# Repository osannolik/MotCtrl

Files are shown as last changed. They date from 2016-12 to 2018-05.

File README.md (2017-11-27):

MotCtrl
=========================== 

A small inverter for brushless motors. 

## Hardware

* Microcontroller STM32F446, ARM Cortex-M4, 180 MHz, FPU
* Power MOSFETs 60 V, 300 A, 1.1 mOhm FDBL0110N60
* High- and low-side gate drivers LM5101A
* Inline phase current sensing using INA240 amplifiers
* Hall-sensor inputs
* Standard servo (PPM/PWM) input
* Motor and board temp sensor (NTC)
* Expansion header for UART/ADC/DAC/SPI/I2C/CAN
* PCB size 45x77 mm

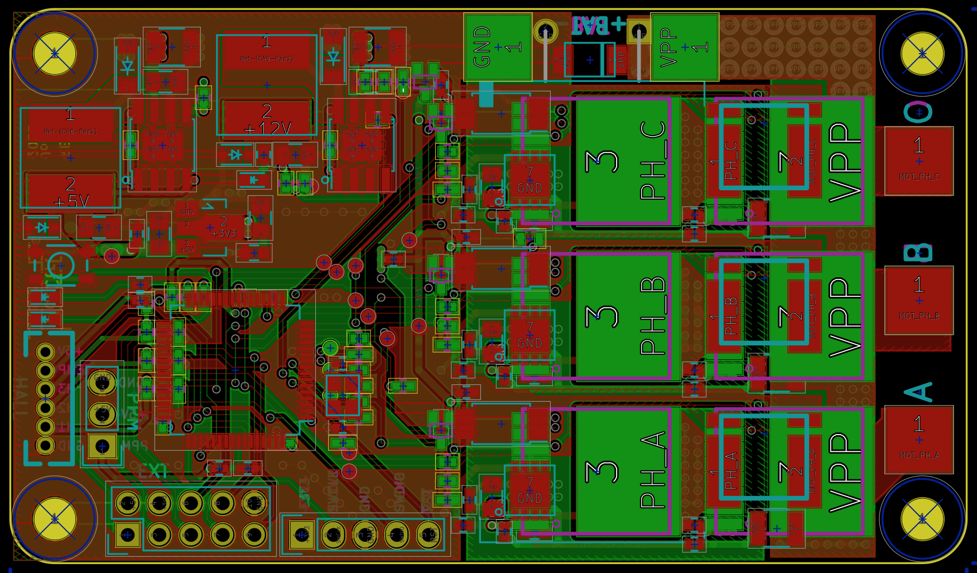
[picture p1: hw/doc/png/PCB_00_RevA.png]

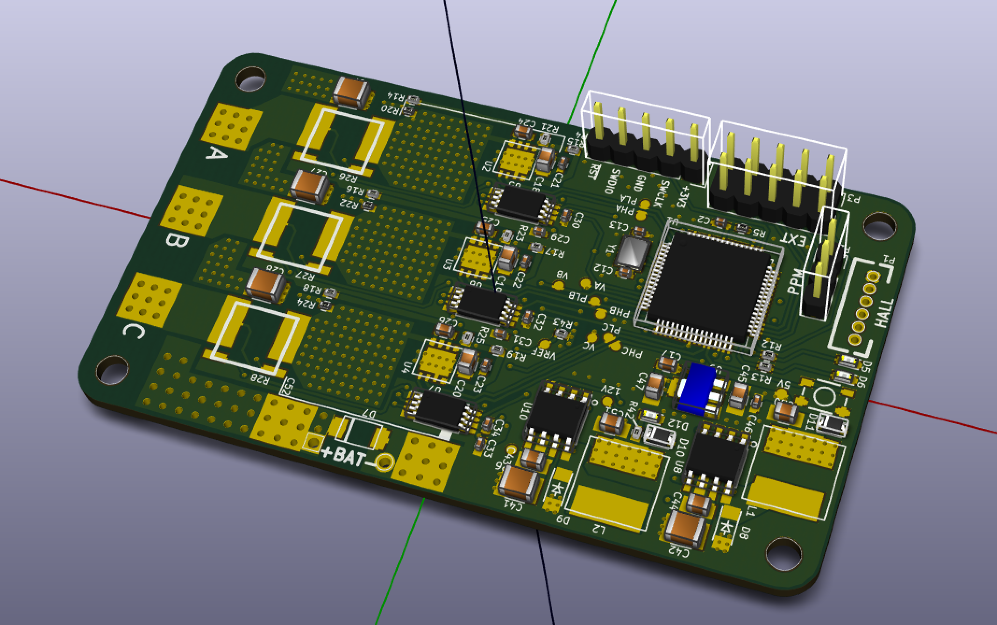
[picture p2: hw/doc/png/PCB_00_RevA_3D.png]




# License
GNU GPLv3 (both hardware and experimental software)

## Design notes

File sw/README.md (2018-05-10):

# Software
This software should be seen as a proof of concept, or as a starting point for developing a complete motor control application.

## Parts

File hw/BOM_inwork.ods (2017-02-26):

Reference | Value | Qty | Digikey | Package
C1 | 10n |  | 1276-1051-1-ND | 0402
C10 | 100n |  | 1276-1001-1-ND | 0402
C11 | 100n |  | 1276-1001-1-ND | 0402
C12 | np |  |  | 0402
C13 | np |  |  | 0402
C14 | 100n |  | 1276-1001-1-ND | 0402
C15 | 100n |  | 1276-1001-1-ND | 0402
C16 | 100n |  | 1276-1001-1-ND | 0402
C17 | 4u7 |  | 1276-2087-1-ND | 0603
C18 | 10u |  | 1276-2872-1-ND | 0805
C19 | 10u |  | 1276-2872-1-ND | 0805
C2 | 4n7 |  | 490-8259-1-ND | 0402
C20 | 10u |  | 1276-2872-1-ND | 0805
C21 | 100n |  | 1276-1001-1-ND | 0402
C22 | 100n |  | 1276-1001-1-ND | 0402
C23 | 100n |  | 1276-1001-1-ND | 0402
C24 | 220n/24V/X7R |  | 445-7408-1-ND | 0603
C25 | 220n/24V/X7R |  | 445-7408-1-ND | 0603
C26 | 220n/24V/X7R |  | 445-7408-1-ND | 0603
C27 | 10u |  | 1276-3388-1-ND | 1210
C28 | 10u |  | 1276-3388-1-ND | 1210
C29 | 100n |  | 1276-1001-1-ND | 0402
C3 | 4n7 |  | 490-8259-1-ND | 0402
C30 | 100n |  | 1276-1001-1-ND | 0402
C31 | 100n |  | 1276-1001-1-ND | 0402
C32 | 100n |  | 1276-1001-1-ND | 0402
C33 | 100n |  | 1276-1001-1-ND | 0402
C34 | 100n |  | 1276-1001-1-ND | 0402
C35 | np |  |  | 0402
C36 | np |  |  | 0402
C37 | np |  |  | 0402
C38 | 1n |  | 1276-1032-1-ND | 0402
C39 | 1n |  | 1276-1032-1-ND | 0402
C4 | 4n7 |  | 490-8259-1-ND | 0402
C40 | 1n |  | 1276-1032-1-ND | 0402
C41 | 10u/50V |  | 1276-3388-1-ND | 1210
C42 | 10u/50V |  | 1276-3388-1-ND | 1210
C43 | 1u/50V |  | 1276-1029-1-ND | 0805
C44 | 1u/50V |  | 1276-1029-1-ND | 0805
C45 | 10u |  | 1276-2872-1-ND | 0805
C46 | 100n |  | 1276-1001-1-ND | 0402
C47 | 22u |  | 490-10511-1-ND | 0805
C48 | 10n/50V |  | 490-4516-1-ND | 0402
C49 | 10n/50V |  | 490-4516-1-ND | 0402
C5 | 4n7 |  | 490-8259-1-ND | 0402
C50 | 22u/10V |  | 490-10511-1-ND | 0805
C51 | 10u/16V |  | 1276-2872-1-ND | 0805
C52 | 2200u/63V1 |  | 493-1130-ND | 7.50, d18.00, h37.50
C6 | 4n7 |  | 490-8259-1-ND | 0402
C7 | 10u |  | 1276-3388-1-ND | 1210
C8 | 2u2 |  | 1276-1469-1-ND | 0402
C9 | 100n |  | 1276-1001-1-ND | 0402
D1 | BAT854SW |  | 568-6027-1-ND | SOT-323
D10 | SP4023 |  | F6758CT-ND | SOD-323
D11 | SP4021 |  | F6272CT-ND | SOD-323
D12 | LED |  | 754-1121-1-ND | LED-0603
D2 | BAT854SW |  | 568-6027-1-ND | SOT-323
D3 | BAT854SW |  | 568-6027-1-ND | SOT-323
D4 | BAT854SW |  | 568-6027-1-ND | SOT-323
D5 | LED |  | 475-2512-1-ND | LED-0603
D6 | LED |  | 754-1121-1-ND | LED-0603
D7 | PTVS51VP1UP |  | 568-5331-1-ND | SOD-128
D8 | SS26FL |  | SS26FLCT-ND | SOD-123F
D9 | SS26FL |  | SS26FLCT-ND | SOD-123F
L1 | 33u/1A |  | SRN8040TA-330MCT-ND | SRN8040TA
L2 | 47u/1A |  | SRN8040TA-470MCT-ND | SRN8040TA
NTC1 | 10k |  | 490-4800-1-ND | 0603
P1 | CONN_01X06 |  | S1211EC-06-ND | Pin header
P2 | CONN_01X03 |  | S1211EC-06-ND | Pin header
P3 | CONN_02X05 |  | S2011EC-05-ND | Pin header
P4 | CONN_01X05 |  | S1211EC-06-ND | Pin header
Q1 | FDBL0110N60 |  | FDBL0110N60CT-ND | MO-299A
Q2 | FDBL0110N60 |  | FDBL0110N60CT-ND | MO-299A
Q3 | FDBL0110N60 |  | FDBL0110N60CT-ND | MO-299A
Q4 | FDBL0110N60 |  | FDBL0110N60CT-ND | MO-299A
Q5 | FDBL0110N60 |  | FDBL0110N60CT-ND | MO-299A
Q6 | FDBL0110N60 |  | FDBL0110N60CT-ND | MO-299A
R1 | 20k |  | P20.0KLCT-ND | 0402
R10 | 10k |  | 311-10.0KLRCT-ND | 0402
R11 | 10k |  | 311-10.0KLRCT-ND | 0402
R12 | 100R |  | P100LCT-ND | 0402
R13 | 100R |  | P100LCT-ND | 0402
R14 | 4R7 |  | 541-4.70LLCT-ND | 0402
R15 | 4R7 |  | 541-4.70LLCT-ND | 0402
R16 | 4R7 |  | 541-4.70LLCT-ND | 0402
R17 | 4R7 |  | 541-4.70LLCT-ND | 0402
R18 | 4R7 |  | 541-4.70LLCT-ND | 0402
R19 | 4R7 |  | 541-4.70LLCT-ND | 0402
R2 | 1k8 |  | P1.80KLCT-ND | 0402
R20 | 33k |  | P33.0KLCT-ND | 0402
R21 | 33k |  | P33.0KLCT-ND | 0402
R22 | 33k |  | P33.0KLCT-ND | 0402
R23 | 33k |  | P33.0KLCT-ND | 0402
R24 | 33k |  | P33.0KLCT-ND | 0402
R25 | 33k |  | P33.0KLCT-ND | 0402
R26 | WSLP2726 / 0.5 mOhm |  | WSLP2726L5000FEA-ND | WSLP2726
R27 | WSLP2726 / 0.5 mOhm |  | WSLP2726L5000FEA-ND | WSLP2726
R28 | WSLP2726 / 0.5 mOhm |  | WSLP2726L5000FEA-ND | WSLP2726
R29 | 33k |  | P33.0KLCT-ND | 0402
R3 | 10k |  | 311-10.0KLRCT-ND | 0402
R30 | 0R |  | 311-0.0JRCT-ND | 0402
R31 | 33k |  | P33.0KLCT-ND | 0402
R32 | 0R |  | 311-0.0JRCT-ND | 0402
R33 | 33k |  | P33.0KLCT-ND | 0402
R34 | 0R |  | 311-0.0JRCT-ND | 0402
R35 | 3k9 |  | P3.90KLCT-ND | 0402
R36 | 3k9 |  | P3.90KLCT-ND | 0402
R37 | 3k9 |  | P3.90KLCT-ND | 0402
R38 | 470k |  | 541-470KLCT-ND | 0402
R39 | 10k |  | 311-10.0KLRCT-ND | 0402
R4 | 2k2 |  | P2.20KLCT-ND | 0402
R40 | 787R |  | P787LCT-ND | 0402
R41 | 1k |  | P1.00KLCT-ND | 0402
R42 | 3k9 |  | P3.90KLCT-ND | 0402
R43 | 0R |  | 311-0.0JRCT-ND | 0402
R5 | 2k2 |  | P2.20KLCT-ND | 0402
R6 | 2k2 |  | P2.20KLCT-ND | 0402
R7 | 2k2 |  | P2.20KLCT-ND | 0402
R8 | 10k |  | 311-10.0KLRCT-ND | 0402
R9 | 10k |  | 311-10.0KLRCT-ND | 0402
SW1 | PTS810 |  | CKN10503CT-ND | PTS810
U1 | STM32F446R(C-E)Tx |  | 497-15376-ND | 64-LQFP
U10 | LM22675-5.0 |  | 296-38092-1-ND | HSOP-8
U2 | LM5101A |  | 296-40235-1-ND | 8-WSON
U3 | LM5101A |  | 296-40235-1-ND | 8-WSON
U4 | LM5101A |  | 296-40235-1-ND | 8-WSON
U5 | INA240A2 |  | 296-45089-1-ND | 8-TSSOP
U6 | INA240A2 |  | 296-45089-1-ND | 8-TSSOP
U7 | INA240A2 |  | 296-45089-1-ND | 8-TSSOP
U8 | LM22675-5.0 |  | 296-38092-1-ND | HSOP-8
U9 | AZ1117CR-3.3 |  | AZ1117CR-3.3TRG1DICT-ND | SOT-89
Y1 | 16 MHz |  | SER4069CT-ND

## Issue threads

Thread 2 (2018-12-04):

R14 power rating

roor, 2018-12-04:
Hello, i find your design quite fascinating, and trying to build something similar. I have question about gate resistors power rating.
In my math it is look like:
Gate voltage is 12V
Gate resistor 4.7Ohm
I_g_resistor = V/R = 12/4.7 = 2.55A
P= I^2*R = 30.56W

Is it correct and do you use such power resistor or it is acceptable to use lower power rating resistor for gates?

thank you for response

roor, 2018-12-06:
Thnx a lot, i knew there was something wrong, since it is just abnormally high power fur such an easy job.

Closed 2018-12-06.

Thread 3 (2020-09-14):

low power STM32 MCU

mkeyno, 2020-09-14:
sorry for open ticket for my question
I was wondering if these code sources could be ported for lower MCU such as STM32F103 series?
if so what would the penalty for the features?

osannolik, 2020-09-14:
The main issue that might cause performance penalty would be if you use an MCU without FPU. However, if I remember correctly I think the early versions of the VESC used floating point arithmetics in the current control loop on an Cortex-M3 without FPU, so I guess it could work.

Closed 2020-10-28.

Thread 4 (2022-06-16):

estimation of total price BOM

nathmo, 2022-06-16:
hi there, i'm comparing open sources brushless design.
Would you have an estimation of the price to build one ?
 i'm looking for a price range so that i compare it to the others i've found. (and it might be nice to put in the specs list)

many thanks in advance

osannolik, 2022-06-18:
The most expensive parts (mcu, fets, current sense etc) sum to approx 90 USD. Adding the rest (passives and cheaper stuff) and cost of manufacturing the pcb I would estimate the total cost to be around 150-200 USD. That is for a one-off build, the cost per unit of course depend on quantity.

However, if you are looking for a tried and proven design to actually build I do not recommend this one. It was a personal hobby project for learning these kind of things and it has not been used in any real world applications.

nathmo, 2022-06-18:
Thanks a lot for the answer. (I probably won't build one. It's just to get an idea of what design exist, what works, what does not and what is worth what price) yours has a few interesting ideas like the current sensing that I didn't see in much design, but it is quite expensive (event tho the price do tend to drop if I make more than one copy)

Closed 2022-06-18.

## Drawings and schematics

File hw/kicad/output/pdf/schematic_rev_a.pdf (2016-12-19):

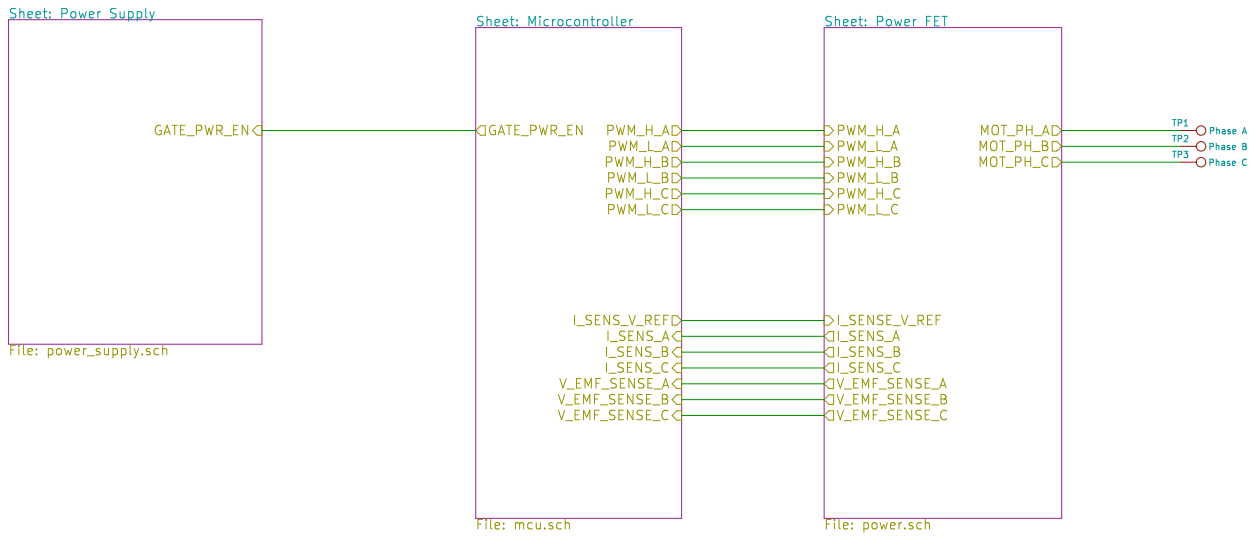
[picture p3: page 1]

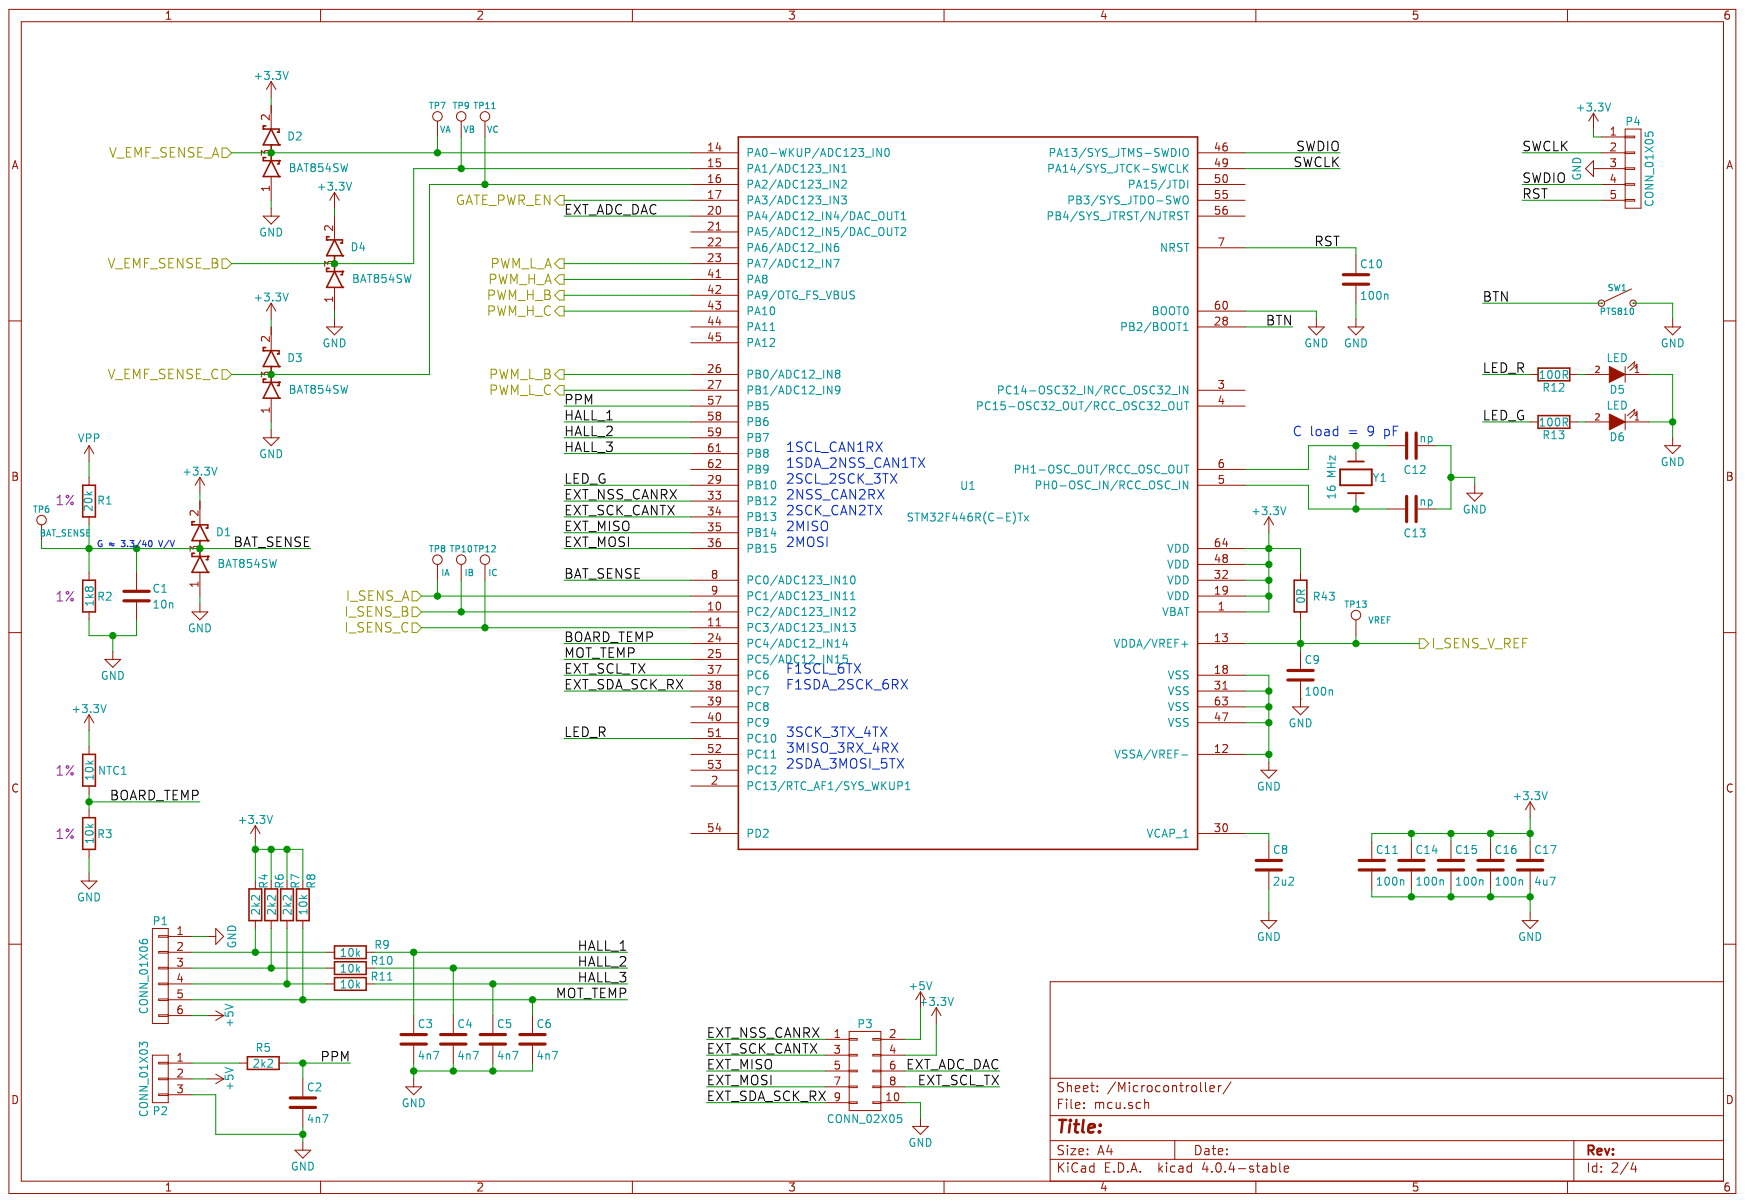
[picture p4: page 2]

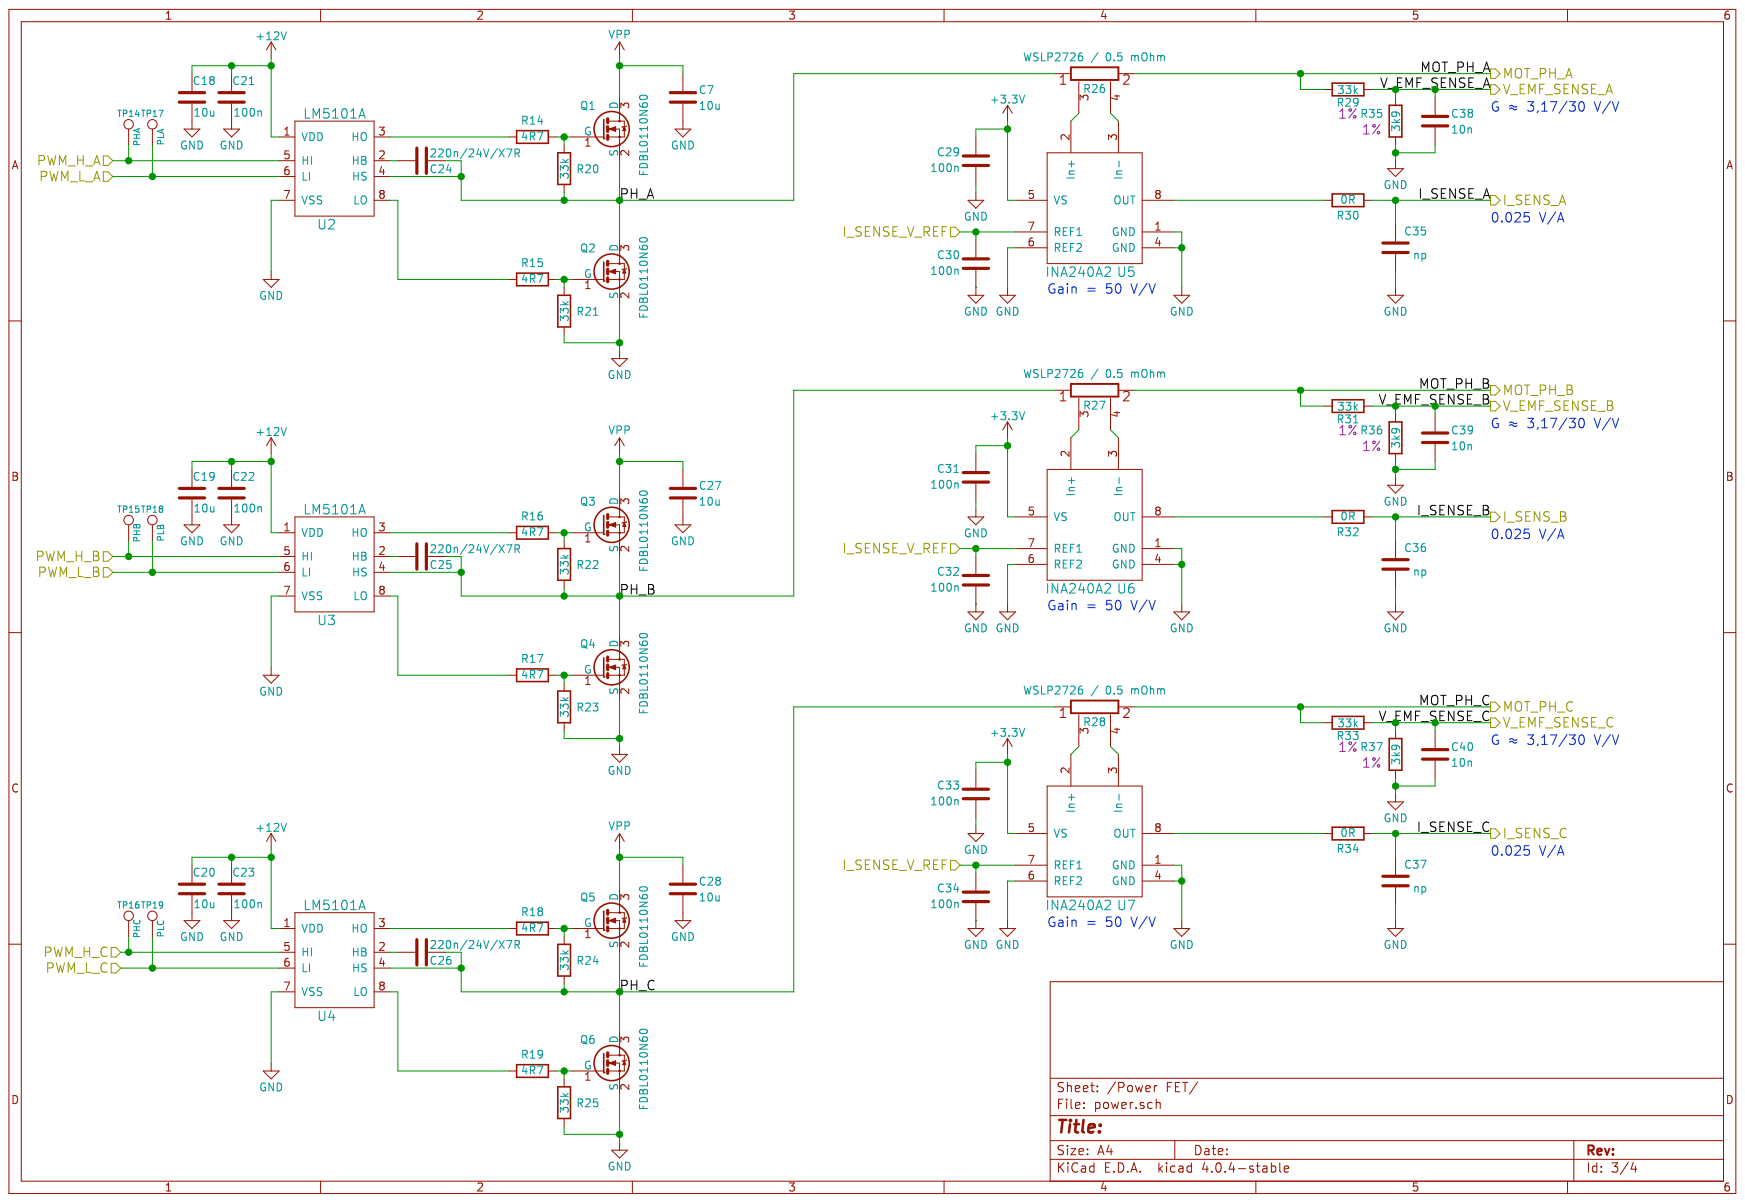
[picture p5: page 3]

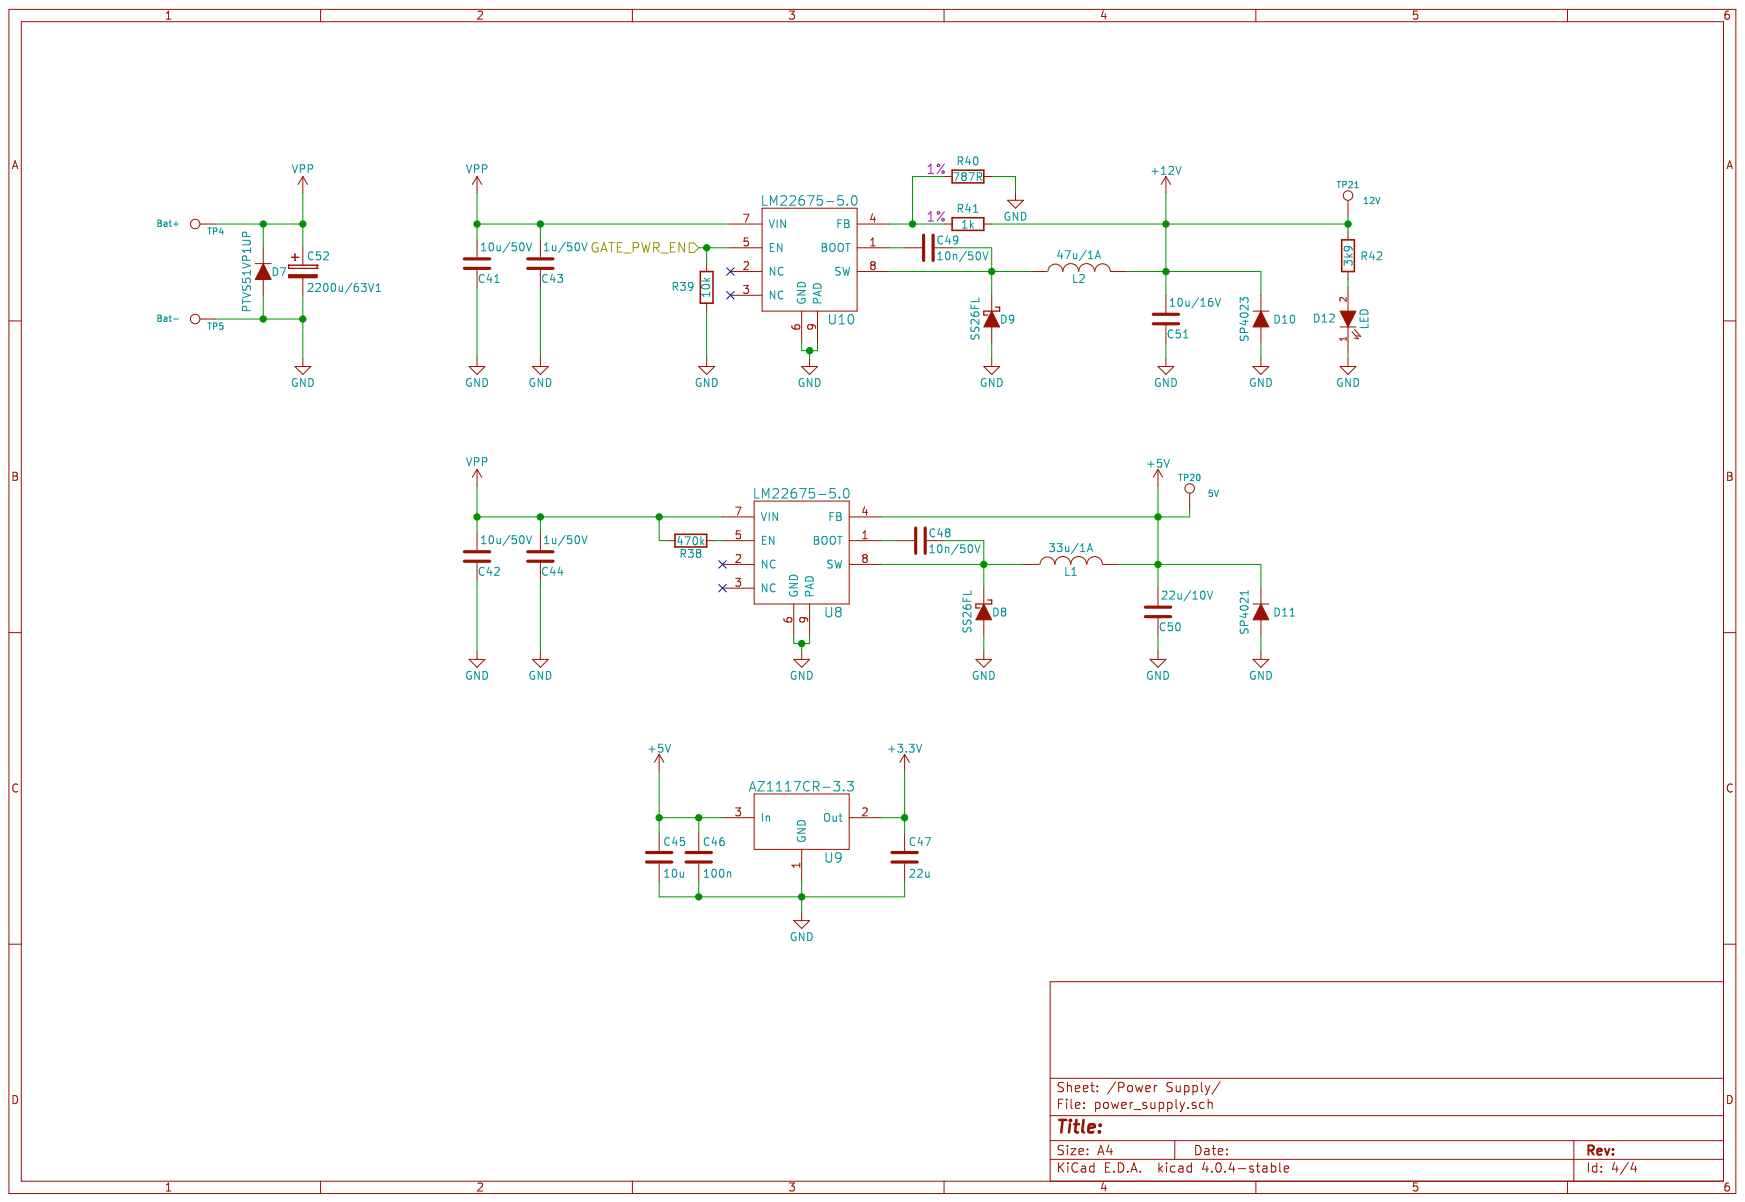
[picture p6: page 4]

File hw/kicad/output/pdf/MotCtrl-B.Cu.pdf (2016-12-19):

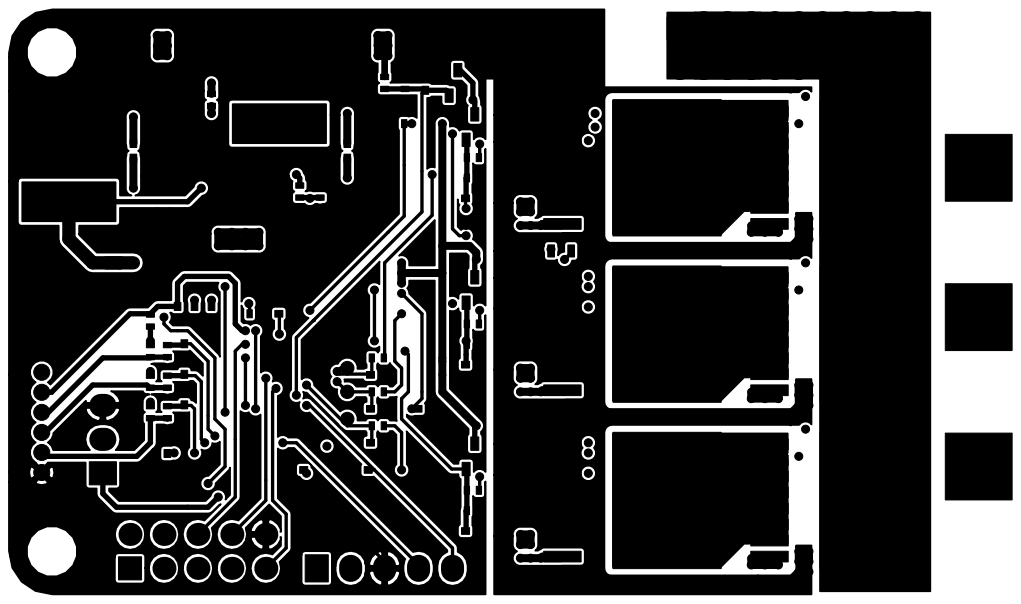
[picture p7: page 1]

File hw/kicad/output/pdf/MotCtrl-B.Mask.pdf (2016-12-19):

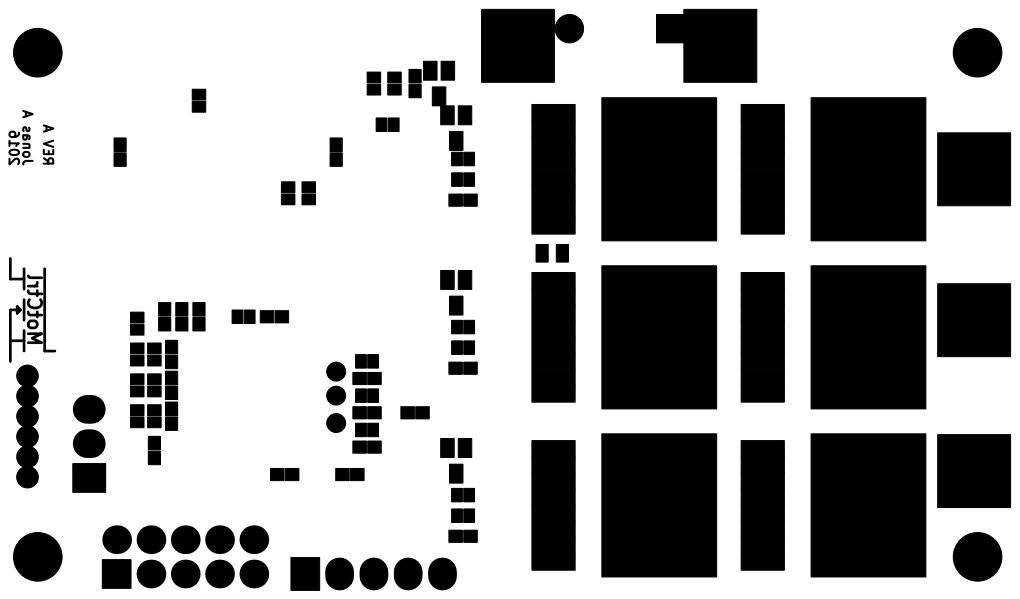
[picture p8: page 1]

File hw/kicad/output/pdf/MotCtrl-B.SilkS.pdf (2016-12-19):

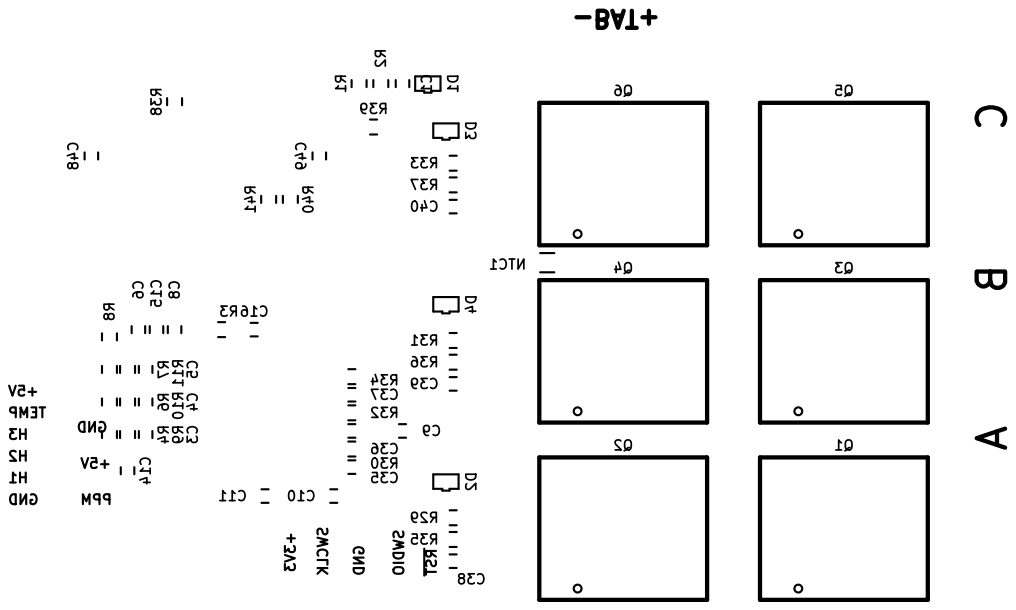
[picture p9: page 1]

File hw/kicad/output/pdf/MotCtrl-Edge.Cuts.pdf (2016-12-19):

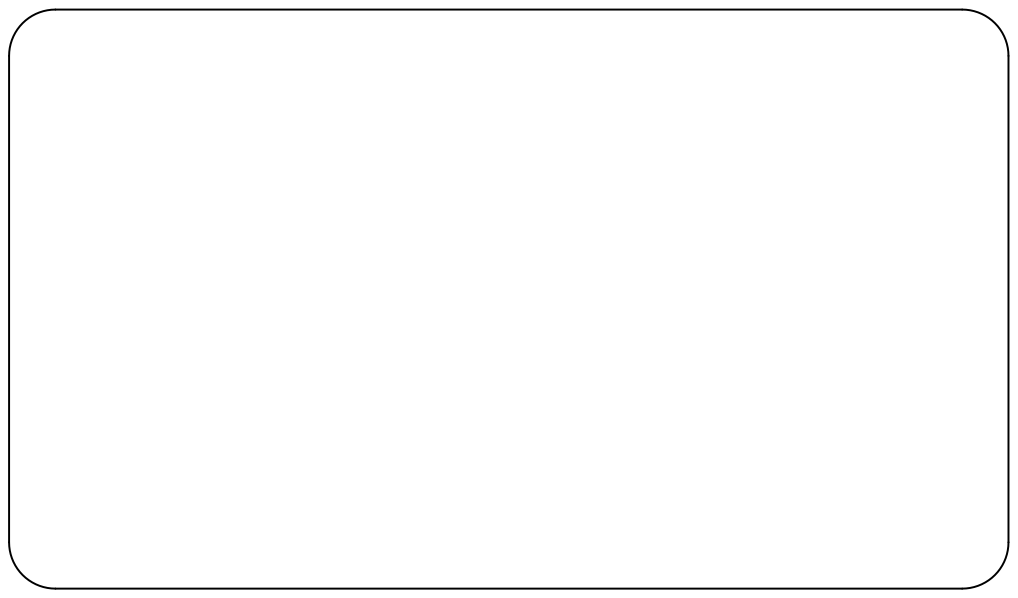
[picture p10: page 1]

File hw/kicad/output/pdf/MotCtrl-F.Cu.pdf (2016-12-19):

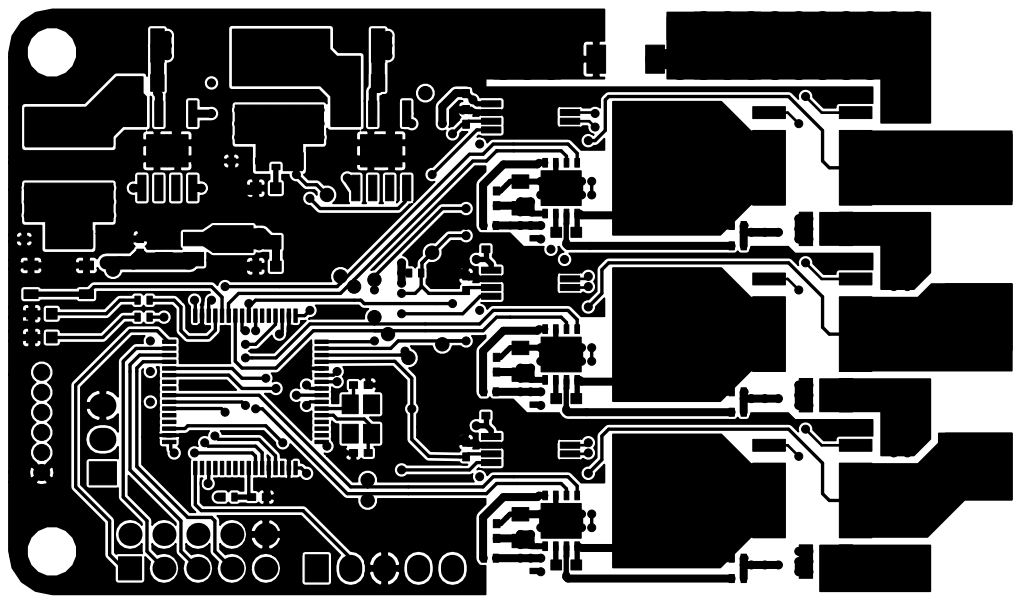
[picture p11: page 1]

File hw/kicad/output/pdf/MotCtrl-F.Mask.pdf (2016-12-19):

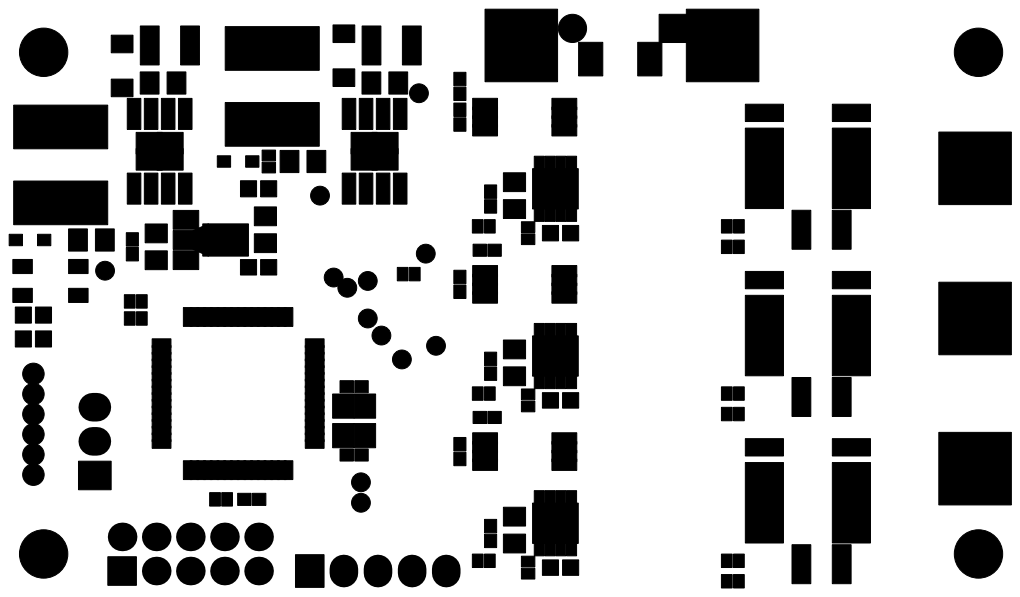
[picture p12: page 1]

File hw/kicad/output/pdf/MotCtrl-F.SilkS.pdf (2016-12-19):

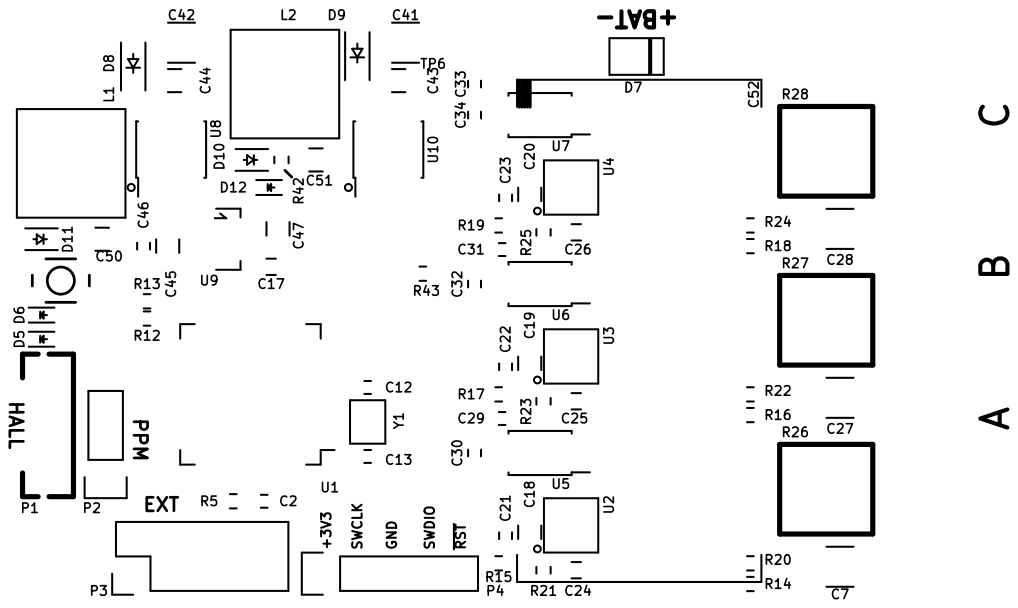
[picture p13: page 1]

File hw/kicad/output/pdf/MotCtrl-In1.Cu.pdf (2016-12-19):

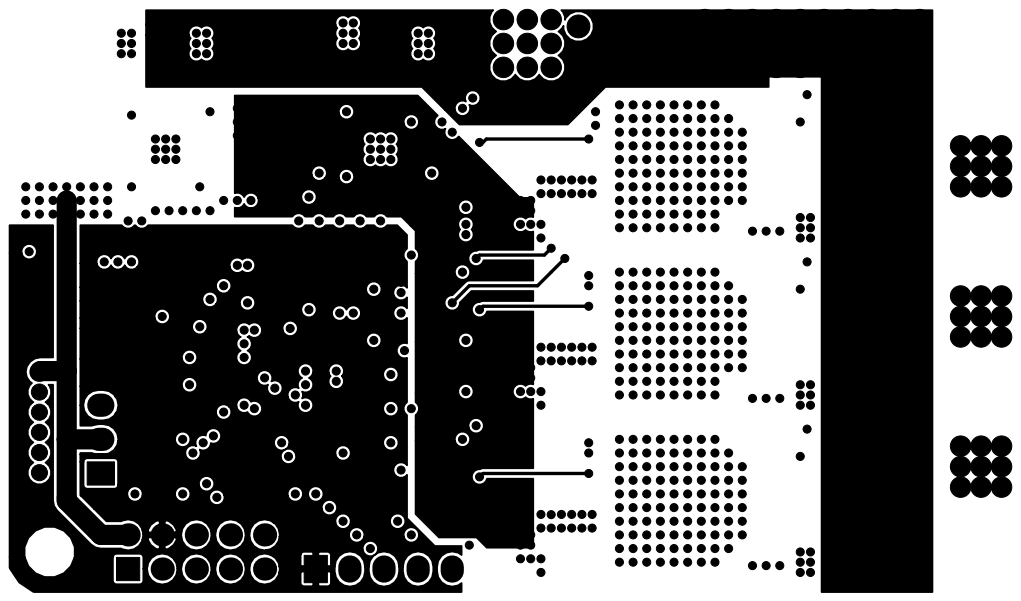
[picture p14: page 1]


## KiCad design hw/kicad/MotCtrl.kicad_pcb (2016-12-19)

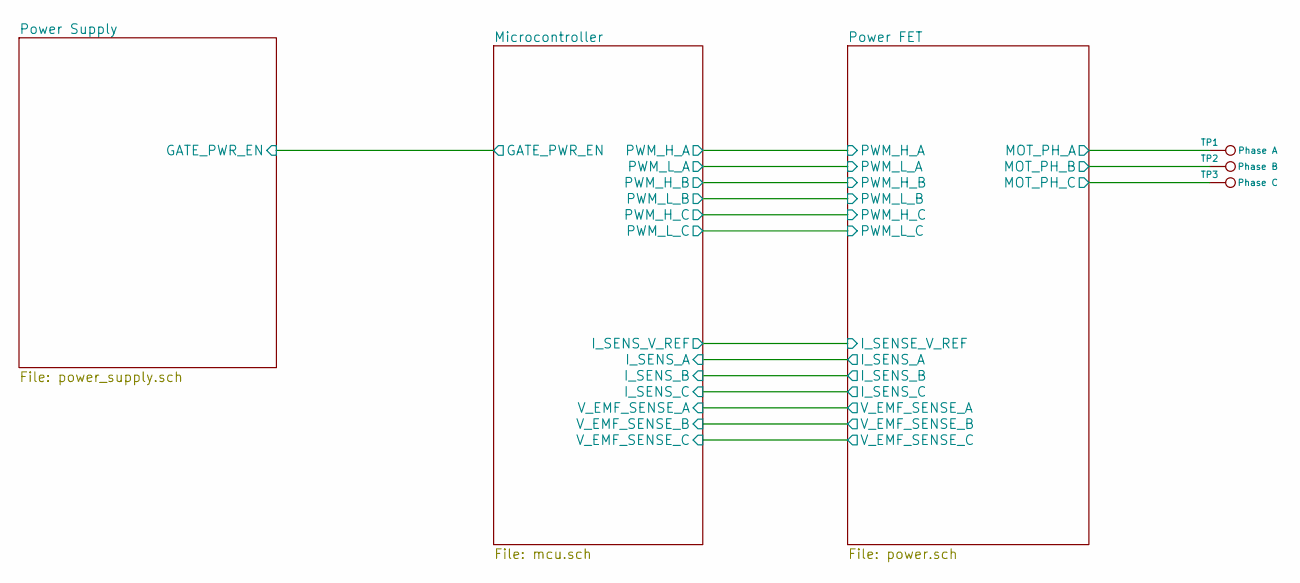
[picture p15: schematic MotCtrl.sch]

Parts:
TP1: Phase A; SolderWirePad_single_SMD_5x5mm
TP2: Phase B; SolderWirePad_single_SMD_5x5mm
TP3: Phase C; SolderWirePad_single_SMD_5x5mm

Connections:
/Power FET/MOT_PH_A: TP1.1; also elsewhere on the board
/Power FET/MOT_PH_B: TP2.1; also elsewhere on the board
/Power FET/MOT_PH_C: TP3.1; also elsewhere on the board

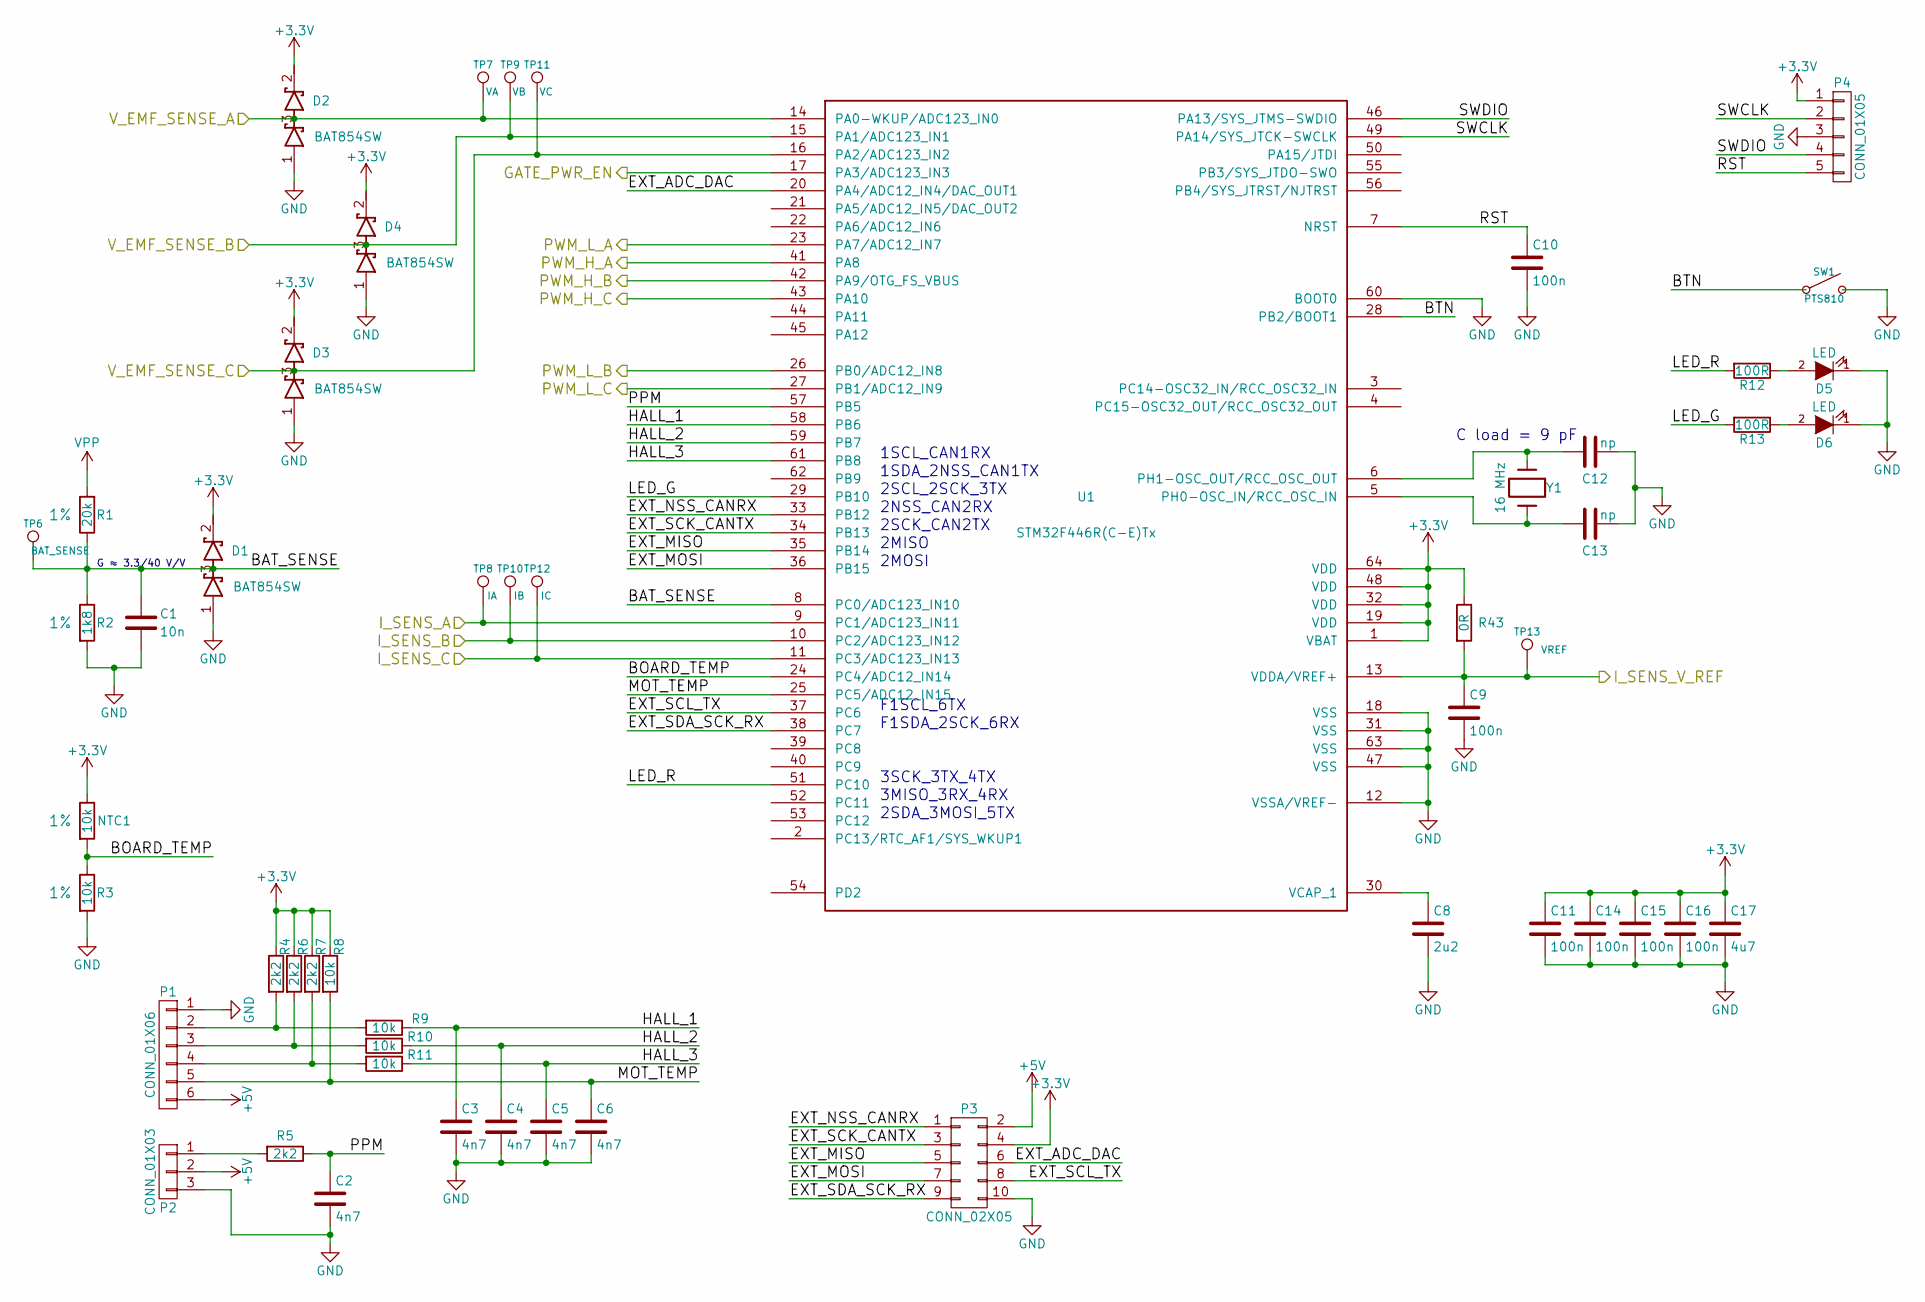
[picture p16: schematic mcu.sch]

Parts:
C1: 10n; C_0402
C2, C3, C4, C5, C6: 4n7; C_0402
C8: 2u2; C_0402
C9, C10, C11, C14, C15, C16: 100n; C_0402
C12, C13: np; C_0402
C17: 4u7; C_0603
D1, D2, D3, D4: BAT854SW; SOT-323
D5, D6: LED; LED_0603
NTC1: 10k; R_0603; Tolerance 1%
P1: CONN_01X06; JST_ZH_B6B-ZR
P2: CONN_01X03; Pin_Header_Straight_1x03
P3: CONN_02X05; Pin_Header_Straight_2x05
P4: CONN_01X05; Pin_Header_Straight_1x05
R1: 20k; R_0402; Tolerance 1%
R2: 1k8; R_0402; Tolerance 1%
R3: 10k; R_0402; Tolerance 1%
R4, R5, R6, R7: 2k2; R_0402
R8, R9, R10, R11: 10k; R_0402
R12, R13: 100R; R_0402
R43: 0R; R_0402
SW1: PTS810
TP6: BAT_SENSE; Measurement_Point_Round-SMD-Pad_Small
TP7: VA; Measurement_Point_Round-SMD-Pad_Small
TP8: IA; Measurement_Point_Round-SMD-Pad_Small
TP9: VB; Measurement_Point_Round-SMD-Pad_Small
TP10: IB; Measurement_Point_Round-SMD-Pad_Small
TP11: VC; Measurement_Point_Round-SMD-Pad_Small
TP12: IC; Measurement_Point_Round-SMD-Pad_Small
TP13: VREF; Measurement_Point_Round-SMD-Pad_Small
U1: STM32F446R(C-E)Tx; LQFP-64_10x10mm_Pitch0.5mm
Y1: 16 MHz; crystal_FA238-TSX3225

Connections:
+3V3: C11.1, C14.1, C15.1, C16.1, C17.1, D1.2 (K), D2.2 (K), D3.2 (K), D4.2 (K), NTC1.1, P3.4, P4.1, R4.1, R6.1, R7.1, R8.1, R43.1, U1.1 (VBAT), U1.19 (VDD), U1.32 (VDD), U1.48 (VDD), U1.64 (VDD); also elsewhere on the board
+5V: P1.6, P2.2, P3.2; also elsewhere on the board
/Microcontroller/BAT_SENSE: C1.1, D1.3 (common), R1.1, R2.1, TP6.1, U1.8 (PC0/ADC123_IN10)
/Microcontroller/BOARD_TEMP: NTC1.2, R3.1, U1.24 (PC4/ADC12_IN14)
/Microcontroller/BTN: SW1.1, SW1.2, U1.28 (PB2/BOOT1)
/Microcontroller/EXT_ADC_DAC: P3.6, U1.20 (PA4/ADC12_IN4/DAC_OUT1)
/Microcontroller/EXT_MISO: P3.5, U1.35 (PB14)
/Microcontroller/EXT_MOSI: P3.7, U1.36 (PB15)
/Microcontroller/EXT_NSS_CANRX: P3.1, U1.33 (PB12)
/Microcontroller/EXT_SCK_CANTX: P3.3, U1.34 (PB13)
/Microcontroller/EXT_SCL_TX: P3.8, U1.37 (PC6)
/Microcontroller/EXT_SDA_SCK_RX: P3.9, U1.38 (PC7)
/Microcontroller/GATE_PWR_EN: U1.17 (PA3/ADC123_IN3); also elsewhere on the board
/Microcontroller/HALL_1: C3.1, R9.1, U1.58 (PB6)
/Microcontroller/HALL_2: C4.1, R10.1, U1.59 (PB7)
/Microcontroller/HALL_3: C5.1, R11.1, U1.61 (PB8)
/Microcontroller/I_SENS_A: TP8.1, U1.9 (PC1/ADC123_IN11); also elsewhere on the board
/Microcontroller/I_SENS_B: TP10.1, U1.10 (PC2/ADC123_IN12); also elsewhere on the board
/Microcontroller/I_SENS_C: TP12.1, U1.11 (PC3/ADC123_IN13); also elsewhere on the board
/Microcontroller/LED_G: R13.2, U1.29 (PB10)
/Microcontroller/LED_R: R12.2, U1.51 (PC10)
/Microcontroller/MOT_TEMP: C6.1, P1.5, R8.2, U1.25 (PC5/ADC12_IN15)
/Microcontroller/PPM: C2.1, R5.1, U1.57 (PB5)
/Microcontroller/PWM_H_A: U1.41 (PA8); also elsewhere on the board
/Microcontroller/PWM_H_B: U1.42 (PA9/OTG_FS_VBUS); also elsewhere on the board
/Microcontroller/PWM_H_C: U1.43 (PA10); also elsewhere on the board
/Microcontroller/PWM_L_A: U1.23 (PA7/ADC12_IN7); also elsewhere on the board
/Microcontroller/PWM_L_B: U1.26 (PB0/ADC12_IN8); also elsewhere on the board
/Microcontroller/PWM_L_C: U1.27 (PB1/ADC12_IN9); also elsewhere on the board
/Microcontroller/RST: C10.1, P4.5, U1.7 (NRST)
/Microcontroller/SWCLK: P4.2, U1.49 (PA14/SYS_JTCK-SWCLK)
/Microcontroller/SWDIO: P4.4, U1.46 (PA13/SYS_JTMS-SWDIO)
/Microcontroller/V_EMF_SENSE_A: D2.3 (common), TP7.1, U1.14 (PA0-WKUP/ADC123_IN0); also elsewhere on the board
/Microcontroller/V_EMF_SENSE_B: D4.3 (common), TP9.1, U1.15 (PA1/ADC123_IN1); also elsewhere on the board
/Microcontroller/V_EMF_SENSE_C: D3.3 (common), TP11.1, U1.16 (PA2/ADC123_IN2); also elsewhere on the board
/Power FET/I_SENSE_V_REF: C9.1, R43.2, TP13.1, U1.13 (VDDA/VREF+); also elsewhere on the board
GND: C1.2, C2.2, C3.2, C4.2, C5.2, C6.2, C8.2, C9.2, C10.2, C11.2, C12.1, C13.1, C14.2, C15.2, C16.2, C17.2, D1.1 (A), D2.1 (A), D3.1 (A), D4.1 (A), D5.1 (K), D6.1 (K), P1.1, P2.3, P3.10, P4.3, R2.2, R3.2, SW1.3, SW1.4, U1.12 (VSSA/VREF-), U1.18 (VSS), U1.31 (VSS), U1.47 (VSS), U1.60 (BOOT0), U1.63 (VSS); also elsewhere on the board
unnamed: C8.1, U1.30 (VCAP_1)
unnamed: C12.2, U1.6 (PH1-OSC_OUT/RCC_OSC_OUT), Y1.1
unnamed: C13.2, U1.5 (PH0-OSC_IN/RCC_OSC_IN), Y1.2
unnamed: D5.2 (A), R12.1
unnamed: D6.2 (A), R13.1
unnamed: P1.2, R4.2, R9.2
unnamed: P1.3, R6.2, R10.2
unnamed: P1.4, R7.2, R11.2
unnamed: P2.1, R5.2
VPP: R1.2; also elsewhere on the board

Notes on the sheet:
C load = 9 pF
G ≈ 3.3/40 V/V
1SCL_CAN1RX
1SDA_2NSS_CAN1TX
2SCL_2SCK_3TX
2NSS_CAN2RX
2SCK_CAN2TX
2MISO
2MOSI
F1SCL_6TX
F1SDA_2SCK_6RX
3SCK_3TX_4TX
3MISO_3RX_4RX
2SDA_3MOSI_5TX

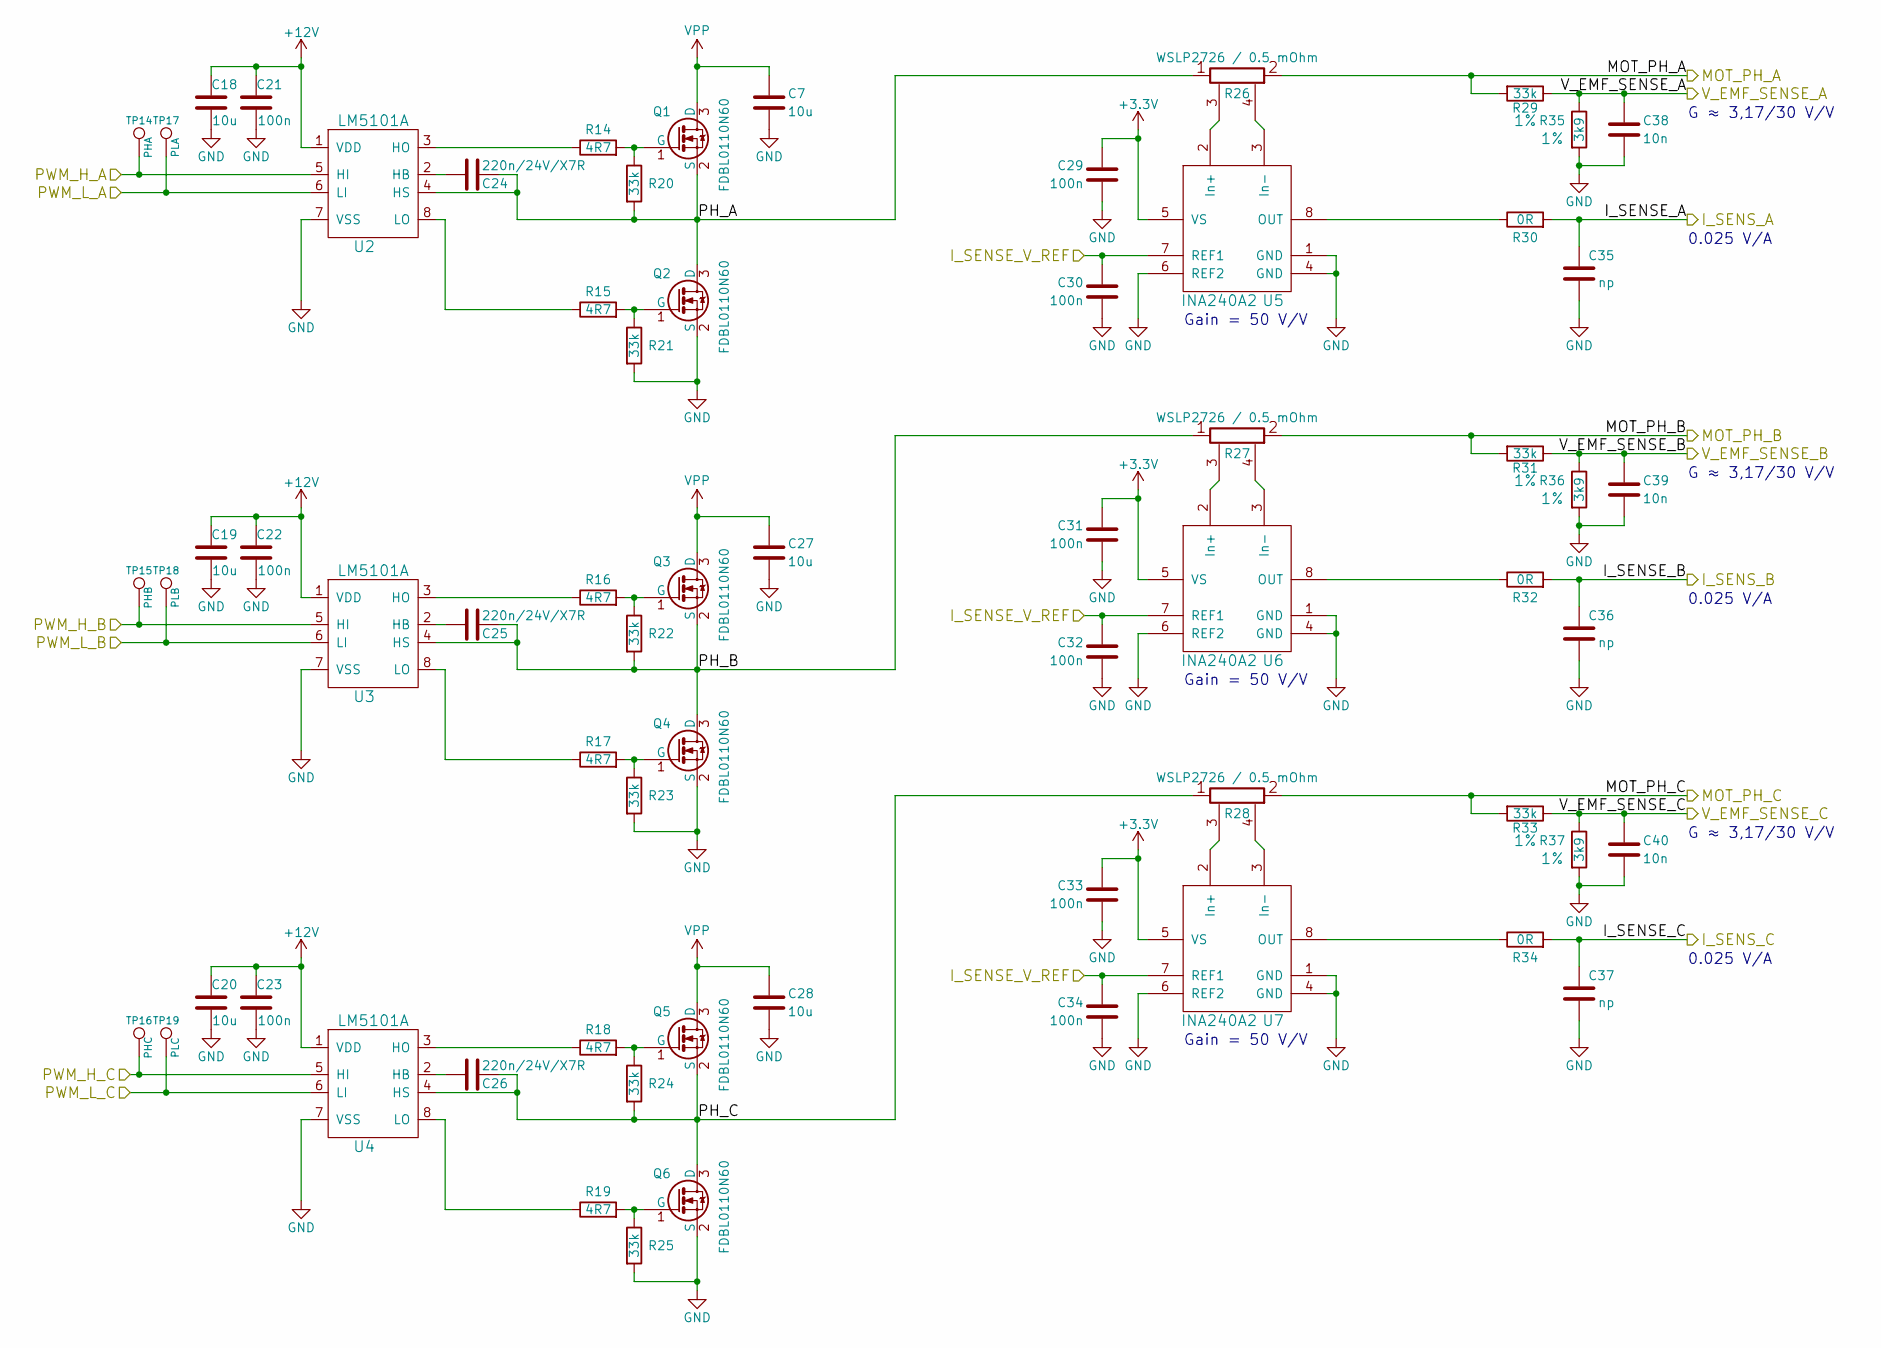
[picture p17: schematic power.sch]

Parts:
C7, C27, C28: 10u; C_1210
C18, C19, C20: 10u; C_0805
C21, C22, C23, C29, C30, C31, C32, C33, C34: 100n; C_0402
C24, C25, C26: 220n/24V/X7R; C_0603
C35, C36, C37: np; C_0402
C38, C39, C40: 10n; C_0402
Q1, Q2, Q3, Q4, Q5, Q6: FDBL0110N60; MO-299A
R14, R15, R16, R17, R18, R19: 4R7; R_0402
R20, R21, R22, R23, R24, R25: 33k; R_0402
R26, R27, R28: WSLP2726 / 0.5 mOhm; WSLP2726
R29, R31, R33: 33k; R_0402; Tolerance 1%
R30, R32, R34: 0R; R_0402
R35, R36, R37: 3k9; R_0402; Tolerance 1%
TP14: PHA; Measurement_Point_Round-SMD-Pad_Small
TP15: PHB; Measurement_Point_Round-SMD-Pad_Small
TP16: PHC; Measurement_Point_Round-SMD-Pad_Small
TP17: PLA; Measurement_Point_Round-SMD-Pad_Small
TP18: PLB; Measurement_Point_Round-SMD-Pad_Small
TP19: PLC; Measurement_Point_Round-SMD-Pad_Small
U2, U3, U4: LM5101A; WSON-8
U5, U6, U7: INA240A2; TSSOP-8_4.4x3mm_Pitch0.65mm

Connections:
+3V3: C29.2, C31.2, C33.2, U5.5 (VS), U6.5 (VS), U7.5 (VS); also elsewhere on the board
+12V: C18.2, C19.2, C20.2, C21.2, C22.2, C23.2, U2.1 (VDD), U3.1 (VDD), U4.1 (VDD); also elsewhere on the board
/Microcontroller/I_SENS_A: C35.2, R30.2; also elsewhere on the board
/Microcontroller/I_SENS_B: C36.2, R32.2; also elsewhere on the board
/Microcontroller/I_SENS_C: C37.2, R34.2; also elsewhere on the board
/Microcontroller/PWM_H_A: TP14.1, U2.5 (HI); also elsewhere on the board
/Microcontroller/PWM_H_B: TP15.1, U3.5 (HI); also elsewhere on the board
/Microcontroller/PWM_H_C: TP16.1, U4.5 (HI); also elsewhere on the board
/Microcontroller/PWM_L_A: TP17.1, U2.6 (LI); also elsewhere on the board
/Microcontroller/PWM_L_B: TP18.1, U3.6 (LI); also elsewhere on the board
/Microcontroller/PWM_L_C: TP19.1, U4.6 (LI); also elsewhere on the board
/Microcontroller/V_EMF_SENSE_A: C38.1, R29.1, R35.1; also elsewhere on the board
/Microcontroller/V_EMF_SENSE_B: C39.1, R31.1, R36.1; also elsewhere on the board
/Microcontroller/V_EMF_SENSE_C: C40.1, R33.1, R37.1; also elsewhere on the board
/Power FET/I_SENSE_V_REF: C30.2, C32.2, C34.2, U5.7 (REF1), U6.7 (REF1), U7.7 (REF1); also elsewhere on the board
/Power FET/MOT_PH_A: R26.2, R29.2; also elsewhere on the board
/Power FET/MOT_PH_B: R27.2, R31.2; also elsewhere on the board
/Power FET/MOT_PH_C: R28.2, R33.2; also elsewhere on the board
/Power FET/PH_A: C24.1, Q1.2 (S), Q2.3 (D), R20.2, R26.1, U2.4 (HS)
/Power FET/PH_B: C25.1, Q3.2 (S), Q4.3 (D), R22.2, R27.1, U3.4 (HS)
/Power FET/PH_C: C26.1, Q5.2 (S), Q6.3 (D), R24.2, R28.1, U4.4 (HS)
GND: C7.2, C18.1, C19.1, C20.1, C21.1, C22.1, C23.1, C27.2, C28.2, C29.1, C30.1, C31.1, C32.1, C33.1, C34.1, C35.1, C36.1, C37.1, C38.2, C39.2, C40.2, Q2.2 (S), Q4.2 (S), Q6.2 (S), R21.2, R23.2, R25.2, R35.2, R36.2, R37.2, U2.7 (VSS), U3.7 (VSS), U4.7 (VSS), U5.1 (GND), U5.4 (GND), U5.6 (REF2), U6.1 (GND), U6.4 (GND), U6.6 (REF2), U7.1 (GND), U7.4 (GND), U7.6 (REF2); also elsewhere on the board
unnamed: C24.2, U2.2 (HB)
unnamed: C25.2, U3.2 (HB)
unnamed: C26.2, U4.2 (HB)
unnamed: Q1.1 (G), R14.2, R20.1
unnamed: Q2.1 (G), R15.2, R21.1
unnamed: Q3.1 (G), R16.2, R22.1
unnamed: Q4.1 (G), R17.2, R23.1
unnamed: Q5.1 (G), R18.2, R24.1
unnamed: Q6.1 (G), R19.2, R25.1
unnamed: R14.1, U2.3 (HO)
unnamed: R15.1, U2.8 (LO)
unnamed: R16.1, U3.3 (HO)
unnamed: R17.1, U3.8 (LO)
unnamed: R18.1, U4.3 (HO)
unnamed: R19.1, U4.8 (LO)
unnamed: R26.3, U5.2 (In+)
unnamed: R26.4, U5.3 (In-)
unnamed: R27.3, U6.2 (In+)
unnamed: R27.4, U6.3 (In-)
unnamed: R28.3, U7.2 (In+)
unnamed: R28.4, U7.3 (In-)
unnamed: R30.1, U5.8 (OUT)
unnamed: R32.1, U6.8 (OUT)
unnamed: R34.1, U7.8 (OUT)
VPP: C7.1, C27.1, C28.1, Q1.3 (D), Q3.3 (D), Q5.3 (D); also elsewhere on the board

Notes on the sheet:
Gain = 50 V/V
0.025 V/A
G ≈ 3,17/30 V/V

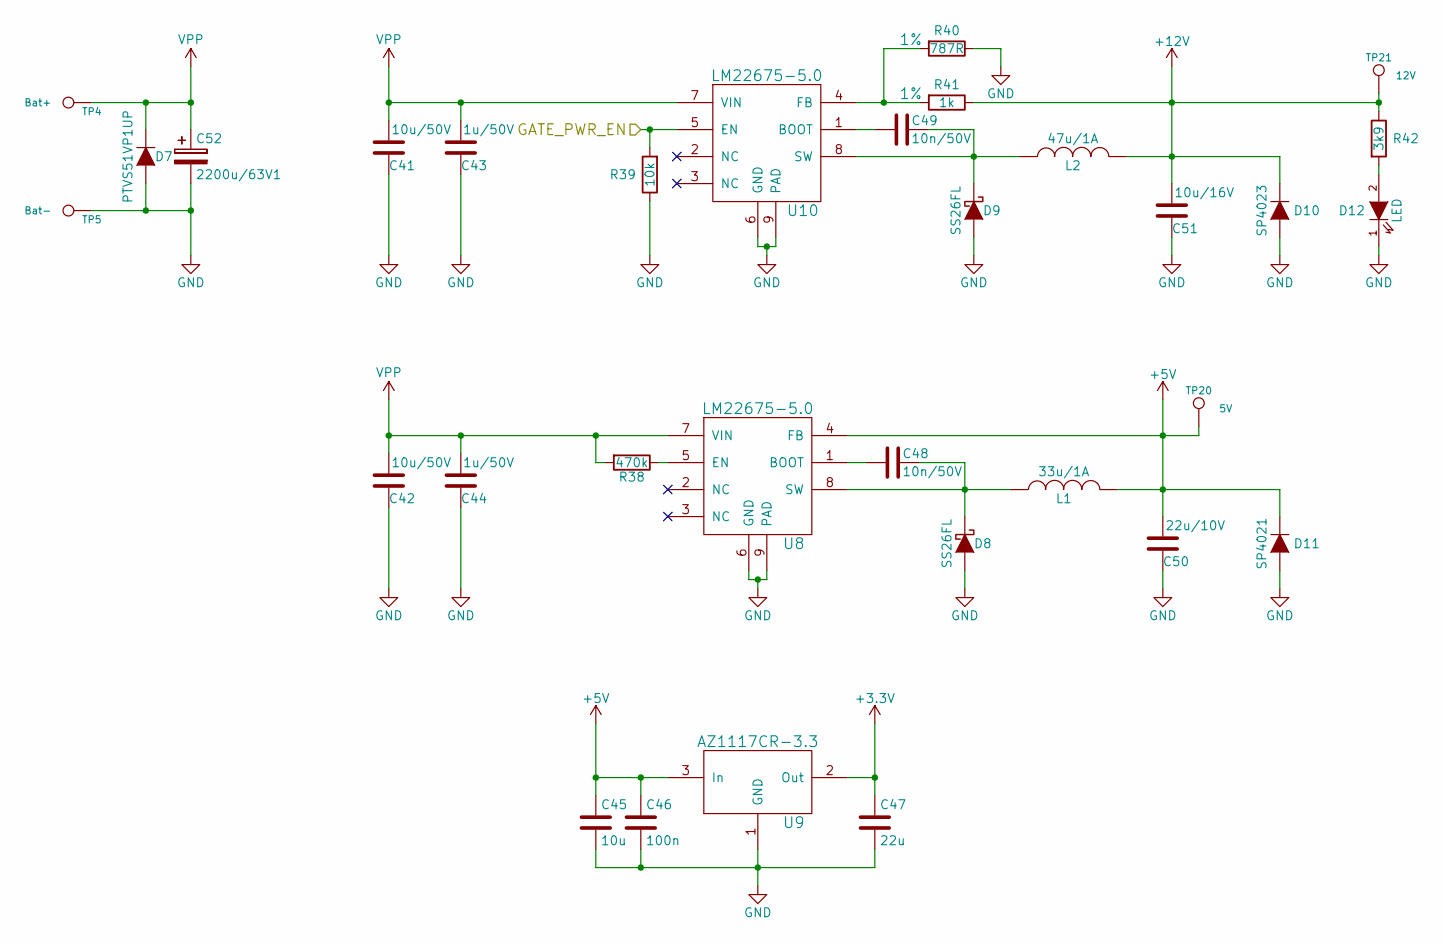
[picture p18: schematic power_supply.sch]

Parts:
C41, C42: 10u/50V; C_1210
C43, C44: 1u/50V; C_0805
C45: 10u; C_0805
C46: 100n; C_0402
C47: 22u; C_0805
C48, C49: 10n/50V; C_0402
C50: 22u/10V; C_0805
C51: 10u/16V; C_0805
C52: 2200u/63V1; C_Radial_D18_L37_P7.5_Angled
D7: PTVS51VP1UP; SOD-128
D8, D9: SS26FL; SOD-123
D10: SP4023; SOD-323
D11: SP4021; SOD-323
D12: LED; LED_0603
L1: 33u/1A; SRN8040TA
L2: 47u/1A; SRN8040TA
R38: 470k; R_0402
R39: 10k; R_0402
R40: 787R; R_0402; Tolerance 1%
R41: 1k; R_0402; Tolerance 1%
R42: 3k9; R_0402
TP4: Bat+; SolderWirePad_single_SMD_5x5mm
TP5: Bat-; SolderWirePad_single_SMD_5x5mm
TP20: 5V; Measurement_Point_Round-SMD-Pad_Small
TP21: 12V; Measurement_Point_Round-SMD-Pad_Small
U8, U10: LM22675-5.0; HSOP-8
U9: AZ1117CR-3.3; SOT89-3_Housing

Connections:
+3V3: C47.1, U9.2 (Out); also elsewhere on the board
+5V: C45.1, C46.1, C50.2, D11.1 (K), L1.2, TP20.1, U8.4 (FB), U9.3 (In); also elsewhere on the board
+12V: C51.2, D10.1 (K), L2.2, R41.1, R42.1, TP21.1; also elsewhere on the board
/Microcontroller/GATE_PWR_EN: R39.2, U10.5 (EN); also elsewhere on the board
GND: C41.1, C42.1, C43.1, C44.1, C45.2, C46.2, C47.2, C50.1, C51.1, C52.2, D7.2 (A), D8.2 (A), D9.2 (A), D10.2 (A), D11.2 (A), D12.1 (K), R39.1, R40.1, TP5.1, U8.6 (GND), U8.9 (PAD), U9.1 (GND), U10.6 (GND), U10.9 (PAD); also elsewhere on the board
unnamed: C48.1, D8.1 (K), L1.1, U8.8 (SW)
unnamed: C48.2, U8.1 (BOOT)
unnamed: C49.1, D9.1 (K), L2.1, U10.8 (SW)
unnamed: C49.2, U10.1 (BOOT)
unnamed: D12.2 (A), R42.2
unnamed: R38.1, U8.5 (EN)
unnamed: R40.2, R41.2, U10.4 (FB)
VPP: C41.2, C42.2, C43.2, C44.2, C52.1, D7.1 (K), R38.2, TP4.1, U8.7 (VIN), U10.7 (VIN); also elsewhere on the board

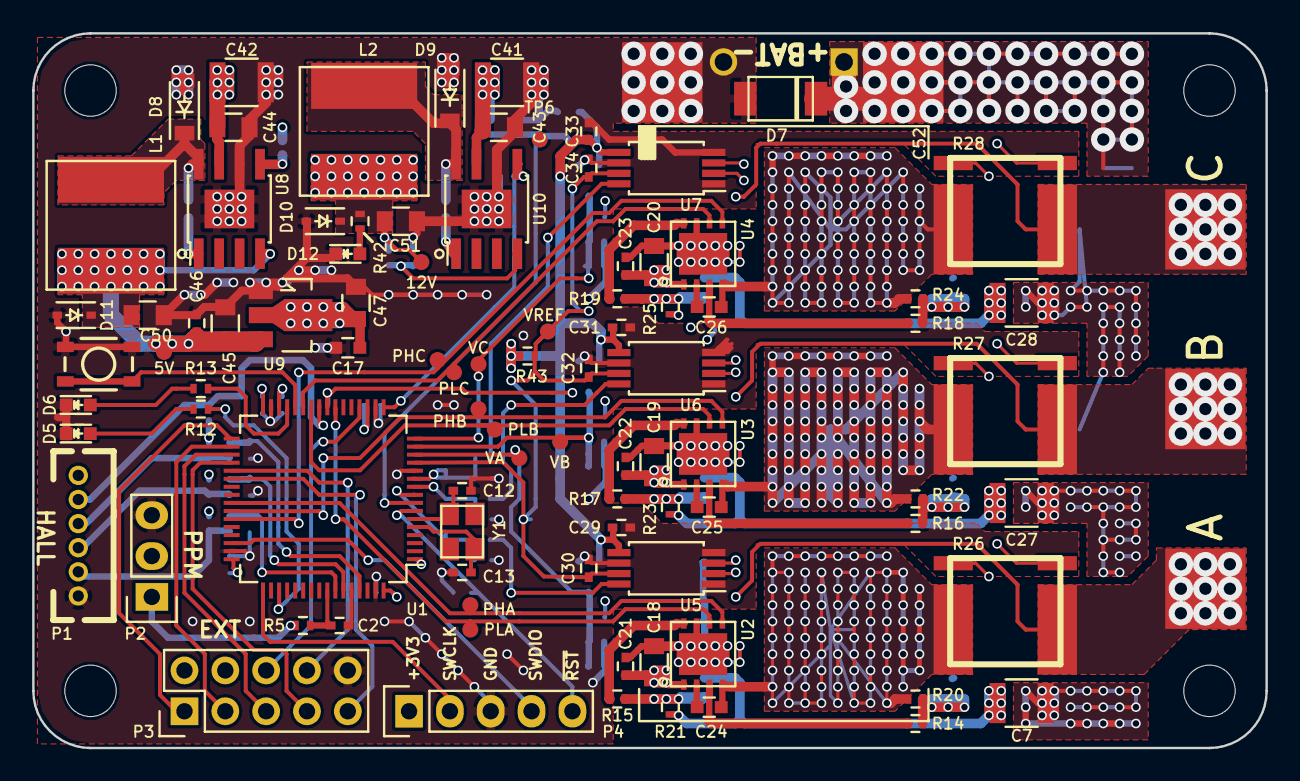
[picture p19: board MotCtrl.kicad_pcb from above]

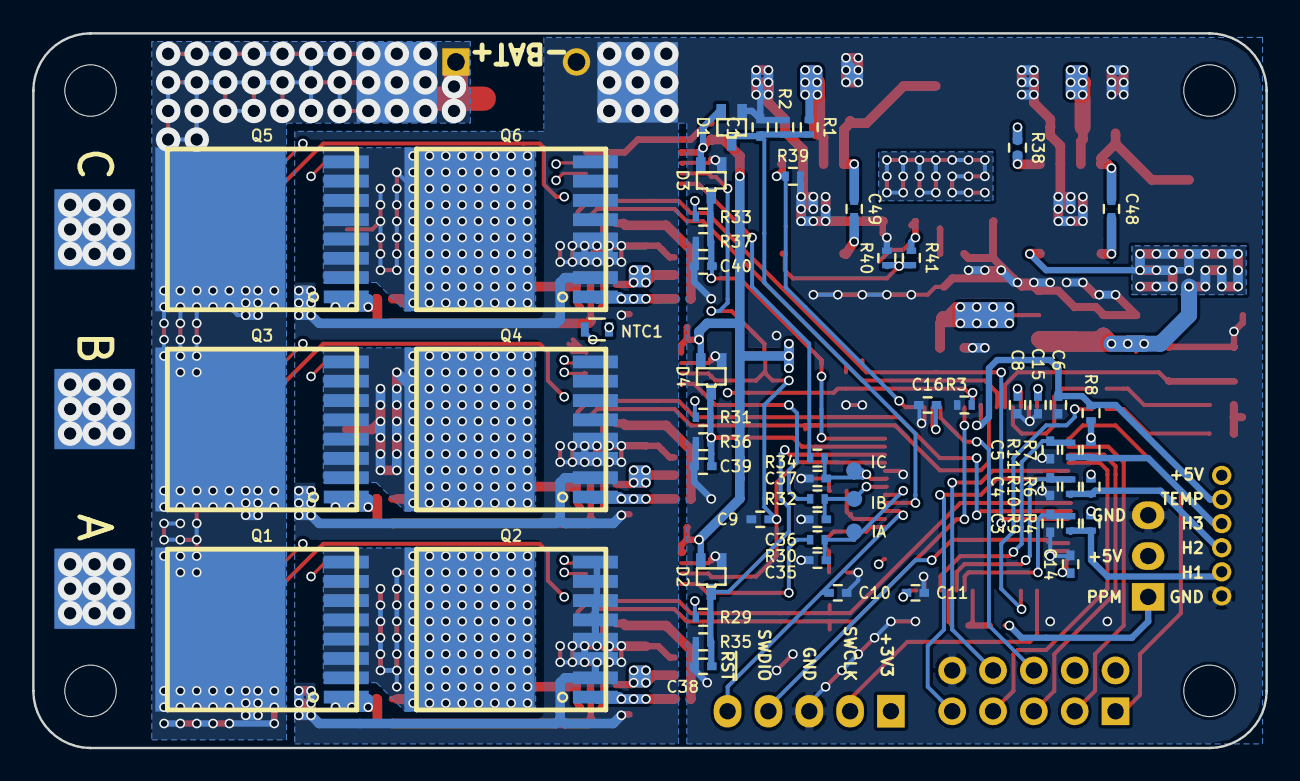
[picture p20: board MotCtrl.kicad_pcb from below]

Board: 4 copper layers, 76.7 x 44.5 mm, 158 parts (62 on the bottom side), 85 nets.

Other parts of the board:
TP1#2: Phase A; SolderWirePad_single_SMD_5x5mm
TP2#2: Phase B; SolderWirePad_single_SMD_5x5mm
TP3#2: Phase C; SolderWirePad_single_SMD_5x5mm
TP4#2: Bat+; SolderWirePad_single_SMD_5x5mm
TP5#2: Bat-; SolderWirePad_single_SMD_5x5mm

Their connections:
/Power FET/MOT_PH_A: TP1#2.1; also elsewhere on the board
/Power FET/MOT_PH_B: TP2#2.1; also elsewhere on the board
/Power FET/MOT_PH_C: TP3#2.1; also elsewhere on the board
GND: TP5#2.1; also elsewhere on the board
VPP: TP4#2.1; also elsewhere on the board

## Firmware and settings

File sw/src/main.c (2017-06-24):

#include "main.h"
#include "utils.h"
#include "rt_kernel.h"
#include "uart.h"
#include "com.h"
#include "calmeas.h"

#include "board.h"
#include "position.h"
#include "pwm.h"
#include "ext.h"
#include "inverter.h"
#include "control.h"
#include "modes.h"
#include "speed_control.h"

static void SystemClock_Config(void);
static void Error_Handler(void);

/* Tasks */
DEFINE_TASK(logger_task, logger_task_handle, "logger_task", 1, 512);
DEFINE_TASK(application_task, application_task_handle, "application_task", 2, 512);

/* Measurements */
CALMEAS_SYMBOL(uint8_t,  m_cpu_utilization_perc, 0, "");

/* Parameters */
// ...

int main(void)
{
  HAL_Init();

  /* Configure the system clock to 180 MHz */
  SystemClock_Config();

  /* Prevent systick from interrupting before kernel is started */
  rt_systick_disable();

  debug_init();

  board_init();
  adc_init();
  pwm_init();

  ext_init();

  modes_init();
  position_init(ENCODER);
  ivtr_init();
  spdctrl_init();
  ctrl_init();

  uart_init();
  com_init();
  calmeas_init();

  /* Start the rtos */
  rt_create_task(&logger_task_handle, NULL);
  rt_create_task(&application_task_handle, NULL);
  rt_start();

  while(1);

  return 0;
}

#if 1
CALMEAS_SYMBOL(float, mdbg_pos_angle, 0, "");
CALMEAS_SYMBOL(float, mdbg_pos_speed, 0, "");

CALMEAS_SYMBOL(float, mdbg_pos_angle_raw, 0, "");
CALMEAS_SYMBOL(float, mdbg_pos_speed_raw, 0, "");
#endif

void application_task(void *p)
{
  (void) p;

  uint32_t lcm_ms;
  uint32_t task_period_ms;

  const uint32_t modes_period_ms    = 8u;
  const uint32_t inverter_period_ms = 4u;
  const uint32_t board_period_ms    = 2u;
  const uint32_t control_period_ms  = 1u;

  task_period_ms = inverter_period_ms;
  lcm_ms = (uint32_t) lcm(task_period_ms, inverter_period_ms);

  task_period_ms = MIN(task_period_ms, modes_period_ms);
  lcm_ms = (uint32_t) lcm(lcm_ms, modes_period_ms);

  task_period_ms = MIN(task_period_ms, board_period_ms);
  lcm_ms = (uint32_t) lcm(lcm_ms, board_period_ms);

  task_period_ms = MIN(task_period_ms, control_period_ms);
  lcm_ms = (uint32_t) lcm(lcm_ms, control_period_ms);

  static uint32_t task_ticker = 0;

  while (1) {

    /* Periodically run step functions */

    if (0u == (task_ticker % board_period_ms)) {
      board_step(board_period_ms);
    }

    if (0u == (task_ticker % modes_period_ms)) {
      modes_step(modes_period_ms);
    }

    if (0u == (task_ticker % control_period_ms)) {
      ctrl_step(control_period_ms);
    }

    if (0u == (task_ticker % inverter_period_ms)) {
      ivtr_step(inverter_period_ms);
    }
#if 0
    mdbg_pos_angle = position_get_angle();
    mdbg_pos_angle_raw = position_get_angle_raw();
    mdbg_pos_speed = position_get_speed();
    mdbg_pos_speed_raw = position_get_speed_raw();
#endif
    m_cpu_utilization_perc = rt_get_cpu_load();

    task_ticker += task_period_ms;
    if (task_ticker >= lcm_ms) {
      task_ticker = 0u;
    }

    rt_periodic_delay(task_period_ms);
  }
}

void logger_task(void *p)
{
  (void) p;

  uint8_t com_period_counter = 0;

  while (1) {

    rt_periodic_delay(1);

    calmeas_handler();

    if (++com_period_counter > 2) {
      com_period_counter = 0;
      com_handler();
    }

  }
}

/**
  * @brief  System Clock Configuration
  *         The system Clock is configured as follow : 
  *            System Clock source            = PLL (HSE)
  *            SYSCLK(Hz)                     = 180000000
  *            HCLK(Hz)                       = 180000000
  *            AHB Prescaler                  = 1
  *            APB1 Prescaler                 = 4
  *            APB2 Prescaler                 = 2
  *            HSE Frequency(Hz)              = 16000000
  *            PLL_M                          = 8 (gives 2 MHz input to PLL which minimizes jitter)
  *            PLL_N                          = 360
  *            PLL_P                          = 4
  *            PLL_Q                          = 15
  *            VDD(V)                         = 3.3
  *            Main regulator output voltage  = Scale1 mode
  *            Flash Latency(WS)              = 5
  * @param  None
  * @retval None
  */
static void SystemClock_Config(void)
{
  RCC_ClkInitTypeDef RCC_ClkInitStruct;
  RCC_OscInitTypeDef RCC_OscInitStruct;
  
  /* Enable Power Control clock */
  __HAL_RCC_PWR_CLK_ENABLE();
  
  /* The voltage scaling allows optimizing the power consumption when the device is 
     clocked below the maximum system frequency, to update the voltage scaling value 
     regarding system frequency refer to product datasheet.  */
  __HAL_PWR_VOLTAGESCALING_CONFIG(PWR_REGULATOR_VOLTAGE_SCALE1);

  /* Enable HSE Oscillator and activate PLL with HSE as source */
  RCC_OscInitStruct.OscillatorType = RCC_OSCILLATORTYPE_HSE;
  RCC_OscInitStruct.HSEState = RCC_HSE_ON;
  RCC_OscInitStruct.PLL.PLLState = RCC_PLL_ON;
  RCC_OscInitStruct.PLL.PLLSource = RCC_PLLSOURCE_HSE;
  RCC_OscInitStruct.PLL.PLLM = 8;
  RCC_OscInitStruct.PLL.PLLN = 360;
  RCC_OscInitStruct.PLL.PLLP = RCC_PLLP_DIV4;
  RCC_OscInitStruct.PLL.PLLQ = 15;
  if(HAL_RCC_OscConfig(&RCC_OscInitStruct) != HAL_OK)
  {
    /* Initialization Error */
    Error_Handler();
  }
  
  /* Select PLL as system clock source and configure the HCLK, PCLK1 and PCLK2 
     clocks dividers */
  RCC_ClkInitStruct.ClockType = (RCC_CLOCKTYPE_SYSCLK | RCC_CLOCKTYPE_HCLK | RCC_CLOCKTYPE_PCLK1 | RCC_CLOCKTYPE_PCLK2);
  RCC_ClkInitStruct.SYSCLKSource = RCC_SYSCLKSOURCE_PLLCLK;
  RCC_ClkInitStruct.AHBCLKDivider = RCC_SYSCLK_DIV1;
  RCC_ClkInitStruct.APB1CLKDivider = RCC_HCLK_DIV4;  
  RCC_ClkInitStruct.APB2CLKDivider = RCC_HCLK_DIV2;  
  if(HAL_RCC_ClockConfig(&RCC_ClkInitStruct, FLASH_LATENCY_5) != HAL_OK)
  {
    /* Initialization Error */
    Error_Handler();
  }

  /* STM32F405x/407x/415x/417x Revision Z devices: prefetch is supported  */
  if (HAL_GetREVID() == 0x1001)
  {
    /* Enable the Flash prefetch */
    __HAL_FLASH_PREFETCH_BUFFER_ENABLE();
  }
}

static void Error_Handler(void)
{
  /* User may add here some code to deal with this error */
  while(1)
  {
  }
}

#ifdef  USE_FULL_ASSERT

/**
  * @brief  Reports the name of the source file and the source line number
  *         where the assert_param error has occurred.
  * @param  file: pointer to the source file name
  * @param  line: assert_param error line source number
  * @retval None
  */
void assert_failed(uint8_t* file, uint32_t line)
{ 
  /* User can add his own implementation to report the file name and line number,
     ex: printf("Wrong parameters value: file %s on line %d\r\n", file, line) */

  /* Infinite loop */
  while (1)
  {
  }
}
#endif

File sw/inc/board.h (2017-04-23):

/*
 * board.h
 *
 *  Created on: 6 feb 2017
 *      Author: osannolik
 */

#ifndef BOARD_H_
#define BOARD_H_

#include "stm32f4xx_hal.h"
#include "adc.h"

#define BOARD_GATE_DRIVER_PIN     GPIO_PIN_3
#define BOARD_GATE_DRIVER_PORT    GPIOA
#define BOARD_GATE_DRIVER_CLK_EN  __HAL_RCC_GPIOA_CLK_ENABLE()

#define BOARD_BUTTON_PIN          GPIO_PIN_2
#define BOARD_BUTTON_PORT         GPIOB
#define BOARD_BUTTON_CLK_EN       __HAL_RCC_GPIOB_CLK_ENABLE()

#define BOARD_V25                 (0.76f)   // MCU temp sensor: voltage at 25 degC
#define BOARD_AVG_SLOPE           (2.5e-3f) // MCU temp sensor: volts per degC

#define BOARD_R1                  (20000.0f)
#define BOARD_R2                  (1800.0f)
#define BOARD_BAT_SENSE_DIVIDER   ((BOARD_R2+BOARD_R1)/BOARD_R2) //approx 40/3.3
#define BOARD_R3                  (10000.0f)
#define BOARD_NTC                 (10000.0f)
#define BOARD_NTC_BETA            (3434.0f)

#define BOARD_R_SHUNT             (0.5e-3f)
#define BOARD_INA240_GAIN         (50.0f) // V/V
#define BOARD_INA240_OFFSET_V     (ADC_VREF*0.5f)


inline float board_ix_volt_to_ampere(float adc_volt);
inline float board_ix_ampere_to_volt(float ix_ampere);

int board_init(void);
void board_step(const uint32_t period_ms);
void board_gate_driver_enable(void);
void board_gate_driver_disable(void);
uint8_t board_button_pressed(void);
float board_bat_voltage(void);
float board_temp_degC(void);
float board_mcu_temp_degC(void);

#endif /* BOARD_H_ */

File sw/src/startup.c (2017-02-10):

/*
 * startup.c
 *
 *  Created on: 18 maj 2012
 *      Author: osannolik
 */

#define MYCPU M4

#include <stdint.h>

/*
 * The next data are defined by the linker script.
 */

extern uint32_t _stext;
extern uint32_t _etext;
extern uint32_t _sdata;
extern uint32_t _edata;
extern uint32_t _sbss;
extern uint32_t _ebss;
extern uint32_t _stack_top;
extern uint32_t _stack_bottom;

#define _STACK_SIZE 0x400 // 1k
// Add stack as symbol to simplify debugging
static uint32_t _stack[_STACK_SIZE] __attribute__ ((aligned(8), used, section(".stack")));

extern int main(void);
extern void SystemInit(void);

void Dummy_Handler(void);

void Reset_Handler(void);

#if MYCPU==M4
/*
 * Cortex M4 core interrupt handlers.
 * Alias to a dummy handler unless otherwise declared.
 */
void HardFault_Handler(void) __attribute__((weak, alias ("Dummy_Handler")));
void NMI_Handler(void) __attribute__((weak, alias ("Dummy_Handler")));
void MemManage_Handler(void) __attribute__((weak, alias ("Dummy_Handler")));
void BusFault_Handler(void) __attribute__((weak, alias ("Dummy_Handler")));
void UsageFault_Handler(void) __attribute__((weak, alias ("Dummy_Handler")));
void SVC_Handler(void) __attribute__((weak, alias ("Dummy_Handler")));
void DebugMon_Handler(void) __attribute__((weak, alias ("Dummy_Handler")));
void PendSV_Handler(void) __attribute__((weak, alias ("Dummy_Handler")));
void SysTick_Handler(void) __attribute__((weak, alias ("Dummy_Handler")));
void WWDG_IRQHandler(void) __attribute__((weak, alias ("Dummy_Handler")));
void PVD_IRQHandler(void) __attribute__((weak, alias ("Dummy_Handler")));
void TAMP_STAMP_IRQHandler(void) __attribute__((weak, alias ("Dummy_Handler")));
void RTC_WKUP_IRQHandler(void) __attribute__((weak, alias ("Dummy_Handler")));
void FLASH_IRQHandler(void) __attribute__((weak, alias ("Dummy_Handler")));
void RCC_IRQHandler(void) __attribute__((weak, alias ("Dummy_Handler")));
void EXTI0_IRQHandler(void) __attribute__((weak, alias ("Dummy_Handler")));
void EXTI1_IRQHandler(void) __attribute__((weak, alias ("Dummy_Handler")));
void EXTI2_IRQHandler(void) __attribute__((weak, alias ("Dummy_Handler")));
void EXTI3_IRQHandler(void) __attribute__((weak, alias ("Dummy_Handler")));
void EXTI4_IRQHandler(void) __attribute__((weak, alias ("Dummy_Handler")));
void DMA1_Stream0_IRQHandler(void) __attribute__((weak, alias ("Dummy_Handler")));
void DMA1_Stream1_IRQHandler(void) __attribute__((weak, alias ("Dummy_Handler")));
void DMA1_Stream2_IRQHandler(void) __attribute__((weak, alias ("Dummy_Handler")));
void DMA1_Stream3_IRQHandler(void) __attribute__((weak, alias ("Dummy_Handler")));
void DMA1_Stream4_IRQHandler(void) __attribute__((weak, alias ("Dummy_Handler")));
void DMA1_Stream5_IRQHandler(void) __attribute__((weak, alias ("Dummy_Handler")));
void DMA1_Stream6_IRQHandler(void) __attribute__((weak, alias ("Dummy_Handler")));
void ADC_IRQHandler(void) __attribute__((weak, alias ("Dummy_Handler")));
void CAN1_TX_IRQHandler(void) __attribute__((weak, alias ("Dummy_Handler")));
void CAN1_RX0_IRQHandler(void) __attribute__((weak, alias ("Dummy_Handler")));
void CAN1_RX1_IRQHandler(void) __attribute__((weak, alias ("Dummy_Handler")));
void CAN1_SCE_IRQHandler(void) __attribute__((weak, alias ("Dummy_Handler")));
void EXTI9_5_IRQHandler(void) __attribute__((weak, alias ("Dummy_Handler")));
void TIM1_BRK_TIM9_IRQHandler(void) __attribute__((weak, alias ("Dummy_Handler")));
void TIM1_UP_TIM10_IRQHandler(void) __attribute__((weak, alias ("Dummy_Handler")));
void TIM1_TRG_COM_TIM11_IRQHandler(void) __attribute__((weak, alias ("Dummy_Handler")));
void TIM1_CC_IRQHandler(void) __attribute__((weak, alias ("Dummy_Handler")));
void TIM2_IRQHandler(void) __attribute__((weak, alias ("Dummy_Handler")));
void TIM3_IRQHandler(void) __attribute__((weak, alias ("Dummy_Handler")));
void TIM4_IRQHandler(void) __attribute__((weak, alias ("Dummy_Handler")));
void I2C1_EV_IRQHandler(void) __attribute__((weak, alias ("Dummy_Handler")));
void I2C1_ER_IRQHandler(void) __attribute__((weak, alias ("Dummy_Handler")));
void I2C2_EV_IRQHandler(void) __attribute__((weak, alias ("Dummy_Handler")));
void I2C2_ER_IRQHandler(void) __attribute__((weak, alias ("Dummy_Handler")));
void SPI1_IRQHandler(void) __attribute__((weak, alias ("Dummy_Handler")));
void SPI2_IRQHandler(void) __attribute__((weak, alias ("Dummy_Handler")));
void USART1_IRQHandler(void) __attribute__((weak, alias ("Dummy_Handler")));
void USART2_IRQHandler(void) __attribute__((weak, alias ("Dummy_Handler")));
void USART3_IRQHandler(void) __attribute__((weak, alias ("Dummy_Handler")));
void EXTI15_10_IRQHandler(void) __attribute__((weak, alias ("Dummy_Handler")));
void RTC_Alarm_IRQHandler(void) __attribute__((weak, alias ("Dummy_Handler")));
void OTG_FS_WKUP_IRQHandler(void) __attribute__((weak, alias ("Dummy_Handler")));
void TIM8_BRK_TIM12_IRQHandler(void) __attribute__((weak, alias ("Dummy_Handler")));
void TIM8_UP_TIM13_IRQHandler(void) __attribute__((weak, alias ("Dummy_Handler")));
void TIM8_TRG_COM_TIM14_IRQHandler(void) __attribute__((weak, alias ("Dummy_Handler")));
void TIM8_CC_IRQHandler(void) __attribute__((weak, alias ("Dummy_Handler")));
void DMA1_Stream7_IRQHandler(void) __attribute__((weak, alias ("Dummy_Handler")));
void FSMC_IRQHandler(void) __attribute__((weak, alias ("Dummy_Handler")));
void SDIO_IRQHandler(void) __attribute__((weak, alias ("Dummy_Handler")));
void TIM5_IRQHandler(void) __attribute__((weak, alias ("Dummy_Handler")));
void SPI3_IRQHandler(void) __attribute__((weak, alias ("Dummy_Handler")));
void UART4_IRQHandler(void) __attribute__((weak, alias ("Dummy_Handler")));
void UART5_IRQHandler(void) __attribute__((weak, alias ("Dummy_Handler")));
void TIM6_DAC_IRQHandler(void) __attribute__((weak, alias ("Dummy_Handler")));
void TIM7_IRQHandler(void) __attribute__((weak, alias ("Dummy_Handler")));
void DMA2_Stream0_IRQHandler(void) __attribute__((weak, alias ("Dummy_Handler")));
void DMA2_Stream1_IRQHandler(void) __attribute__((weak, alias ("Dummy_Handler")));
void DMA2_Stream2_IRQHandler(void) __attribute__((weak, alias ("Dummy_Handler")));
void DMA2_Stream3_IRQHandler(void) __attribute__((weak, alias ("Dummy_Handler")));
void DMA2_Stream4_IRQHandler(void) __attribute__((weak, alias ("Dummy_Handler")));
void ETH_IRQHandler(void) __attribute__((weak, alias ("Dummy_Handler")));
void ETH_WKUP_IRQHandler(void) __attribute__((weak, alias ("Dummy_Handler")));
void CAN2_TX_IRQHandler(void) __attribute__((weak, alias ("Dummy_Handler")));
void CAN2_RX0_IRQHandler(void) __attribute__((weak, alias ("Dummy_Handler")));
void CAN2_RX1_IRQHandler(void) __attribute__((weak, alias ("Dummy_Handler")));
void CAN2_SCE_IRQHandler(void) __attribute__((weak, alias ("Dummy_Handler")));
void OTG_FS_IRQHandler(void) __attribute__((weak, alias ("Dummy_Handler")));
void DMA2_Stream5_IRQHandler(void) __attribute__((weak, alias ("Dummy_Handler")));
void DMA2_Stream6_IRQHandler(void) __attribute__((weak, alias ("Dummy_Handler")));
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

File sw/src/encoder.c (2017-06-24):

/*
 * encoder.c
 *
 *  Created on: 26 maj 2017
 *      Author: osannolik
 */

#include "encoder.h"
#include "math.h"

#define SPEED_COUNTER_MAX (0xFFFFu)

static volatile uint8_t encoder_capture_overflow = 0;

static const float counts_per_revolution = 4 * ENCODER_PPR; // x4 due to counting at all pulse edges

static float speed_timer_resolution_s;
static TIM_HandleTypeDef encoder_timer;
static TIM_HandleTypeDef speed_timer;

int encoder_init(void)
{
  GPIO_InitTypeDef GPIOinitstruct;

  __HAL_RCC_TIM4_CLK_ENABLE();

  GPIOinitstruct.Mode      = GPIO_MODE_AF_PP;
  GPIOinitstruct.Pull      = GPIO_NOPULL;
  GPIOinitstruct.Speed     = GPIO_SPEED_HIGH;
  GPIOinitstruct.Alternate = GPIO_AF2_TIM4;

  ENCODER_A_CLK_EN;
  GPIOinitstruct.Pin = ENCODER_A_PIN;
  HAL_GPIO_Init(ENCODER_A_PORT, &GPIOinitstruct);

  ENCODER_B_CLK_EN;
  GPIOinitstruct.Pin = ENCODER_B_PIN;
  HAL_GPIO_Init(ENCODER_B_PORT, &GPIOinitstruct);

#if 0
  ENCODER_INDEX_CLK_EN;
  GPIOinitstruct.Pin = ENCODER_INDEX_PIN;
  HAL_GPIO_Init(ENCODER_INDEX_PORT, &GPIOinitstruct);
#endif

  /* Initialize TIM4 and TIM3 peripheral as follows:
   *
   * TIM4 is configured in encoder mode.
   * The timer's counter will increment/decrement on all edges of both
   * encoder signal A and B, meaning the counter will reach 4*ppr after
   * one full revolution.
   *
   * Speed is measured by configuring TIM4 as Master and TIM3 as Slave:
   *   - TRGO of TIM4 is set to CC1 which pulses on the rising edge of
   *     encoder input A, giving ppr pulses per revolution, NOT 4*ppr.
   *   - Slave TIM3 is set to capture and reset based on TRC = TRGO
   *
   * Configuration:
   *   APB1 is the clock source = 2*APB1 (2*45 MHz)
   *   Using a prescaler of 1 and using all 16 bits yields:
   *   - Resolution = 1 / 90 MHz = 11.1 ns
   *   - Time until overflow = 2^16 / 90 MHz = 728 us
   *
   * T = 60/ppr/rpm => d/dT rpm = -ppr/60 * rpm^2
   *
   * If ppr = 2048:
   * this allows for a speed down to 40 rpm before an overflow occurs.
   * At 10000 rpm, the resolution will be approx 11.1 ns * 2048/60 * 10000^2 = 38 rpm
   *
   * An increased prescaler allows for lower speed operation, but gives worse resolution.
   */

  /* Encoder timer: Encoder Mode */
  encoder_timer.Instance               = TIM4;
  encoder_timer.Init.Period            = (uint32_t) counts_per_revolution - 1; 
  encoder_timer.Init.Prescaler         = 0;
  encoder_timer.Init.ClockDivision     = 0;
  encoder_timer.Init.CounterMode       = TIM_COUNTERMODE_UP;
  encoder_timer.Init.RepetitionCounter = 0;

  TIM_Encoder_InitTypeDef timer_config;
  timer_config.EncoderMode  = TIM_ENCODERMODE_TI12;
  timer_config.IC1Polarity  = TIM_ICPOLARITY_RISING;
  timer_config.IC1Selection = TIM_ICSELECTION_DIRECTTI;
  timer_config.IC1Prescaler = TIM_ICPSC_DIV1;
  timer_config.IC1Filter    = 0;
  timer_config.IC2Polarity  = TIM_ICPOLARITY_RISING;
  timer_config.IC2Selection = TIM_ICSELECTION_DIRECTTI;
  timer_config.IC2Prescaler = TIM_ICPSC_DIV1;
  timer_config.IC2Filter    = 0;

  HAL_TIM_Encoder_Init(&encoder_timer, &timer_config);

  /* Encoder timer: TRGO = Compare Pulse (CC1IF) */
  TIM_MasterConfigTypeDef master_config;
  master_config.MasterOutputTrigger = TIM_TRGO_OC1;
  master_config.MasterSlaveMode     = TIM_MASTERSLAVEMODE_ENABLE;
  HAL_TIMEx_MasterConfigSynchronization(&encoder_timer, &master_config);

  /* Speed timer: Trigger reset and capture at TRC */
  __HAL_RCC_TIM3_CLK_ENABLE();

  const uint32_t prescaler = 1u;
  speed_timer_resolution_s = ((float) prescaler) / ((float) 2.0f * HAL_RCC_GetPCLK1Freq());
  
  speed_timer.Instance               = TIM3;
  speed_timer.Init.Period            = SPEED_COUNTER_MAX;
  speed_timer.Init.Prescaler         = prescaler - 1;
  speed_timer.Init.ClockDivision     = 0;
  speed_timer.Init.CounterMode       = TIM_COUNTERMODE_UP;
  speed_timer.Init.RepetitionCounter = 0;

  HAL_TIM_Base_Init(&speed_timer);

  TIM_SlaveConfigTypeDef slave_config;
  slave_config.SlaveMode        = TIM_SLAVEMODE_RESET;
  slave_config.InputTrigger     = TIM_TS_ITR3; // TRC = TRGO of TIM4
  slave_config.TriggerPolarity  = TIM_TRIGGERPOLARITY_RISING;
  slave_config.TriggerPrescaler = TIM_TRIGGERPRESCALER_DIV1;
  slave_config.TriggerFilter    = 0;

  HAL_TIM_SlaveConfigSynchronization(&speed_timer, &slave_config);

  TIM_IC_InitTypeDef ic_config;
  ic_config.ICSelection = TIM_ICSELECTION_TRC;
  ic_config.ICPolarity  = TIM_ICPOLARITY_RISING;
  ic_config.ICPrescaler = TIM_ICPSC_DIV1;
  ic_config.ICFilter    = 0;
  HAL_TIM_IC_ConfigChannel(&speed_timer, &ic_config, TIM_CHANNEL_1);

  HAL_TIM_Encoder_Start(&encoder_timer, TIM_CHANNEL_ALL);

  speed_timer.Instance->CR1 |= 0x4u; // Only counter overflow/underflow generates an update interrupt
  __HAL_TIM_ENABLE_IT(&speed_timer, TIM_IT_UPDATE);
  __HAL_TIM_ENABLE_IT(&speed_timer, TIM_IT_CC1);

  NVIC_SetPriority(TIM3_IRQn, ENCODER_IRQ_PRIO);
  NVIC_EnableIRQ(TIM3_IRQn);

  HAL_TIM_IC_Start_IT(&speed_timer, TIM_CHANNEL_1);

  return 0;
}

void TIM3_IRQHandler(void)
{
  /* Capture event: ISR only needed to detect when overflow is over */
  if (__HAL_TIM_GET_FLAG(&speed_timer, TIM_FLAG_CC1) && \
      __HAL_TIM_GET_IT_SOURCE(&speed_timer, TIM_IT_CC1)) {
    __HAL_TIM_CLEAR_IT(&speed_timer, TIM_IT_CC1);

    encoder_capture_overflow = 0;

    __HAL_TIM_ENABLE_IT(&speed_timer, TIM_IT_UPDATE);
    __HAL_TIM_DISABLE_IT(&speed_timer, TIM_IT_CC1);
  }

  /* Speed timer overflow */
  if(__HAL_TIM_GET_FLAG(&speed_timer, TIM_FLAG_UPDATE) && \
     __HAL_TIM_GET_IT_SOURCE(&speed_timer, TIM_IT_UPDATE)) {
    __HAL_TIM_CLEAR_IT(&speed_timer, TIM_FLAG_UPDATE);

    encoder_capture_overflow = 1;

    __HAL_TIM_ENABLE_IT(&speed_timer, TIM_IT_CC1);
    __HAL_TIM_DISABLE_IT(&speed_timer, TIM_IT_UPDATE);
  }
}

float encoder_get_direction(void)
{
  if (encoder_capture_overflow) {
    return 0.0f;
  } else if (__HAL_TIM_IS_TIM_COUNTING_DOWN(&encoder_timer)) {
    return -1.0f;
  } else {
    return 1.0f;
  }
}

float encoder_get_speed_raw_radps(void)
{
  const float t = speed_timer_resolution_s * (float) HAL_TIM_ReadCapturedValue(&speed_timer, TIM_CHANNEL_1);

  return encoder_get_direction() * 2.0f*PI / ((float) ENCODER_PPR * t);
}

float encoder_get_angle_rad(void)
{
  return ((float) encoder_timer.Instance->CNT)*2.0f*PI/counts_per_revolution;
}

float encoder_get_angle_deg(void)
{
  return ((float) encoder_timer.Instance->CNT)*360.0f/counts_per_revolution;
}

void encoder_set_angle_rad(float angle0)
{
  angle0 = wrap_to_range_f(0.0f, 2.0f*PI, angle0);
  const float set_counter = roundf(angle0 * counts_per_revolution/(2.0f*PI));
  encoder_set_counter((uint32_t) set_counter);
}

void encoder_set_angle_deg(const float angle0)
{
  encoder_set_angle_rad(DEG_TO_RAD(angle0));
}

uint32_t encoder_get_counter(void)
{
  return encoder_timer.Instance->CNT;
}

void encoder_set_counter(const uint32_t cnt0)
{
  encoder_timer.Instance->CNT = (uint32_t) wrap_to_range_i(0, (int) counts_per_revolution, cnt0);
}

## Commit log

2016-10-29 Started kicad project
    [MotCtrl.kicad_pcb, MotCtrl.sch, mcu.sch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]
2016-10-30 First steps on gate driver circuit
    [MotCtrl.sch, mcu.sch, power.sch]
2016-11-04 Added power mosfet footprint
    [mcu.sch, power.sch]
2016-11-04 Some more work on the FET-stage
    [MotCtrl.sch, mcu.sch, power.sch]
2016-11-05 More power work
    [MotCtrl.sch, mcu.sch, power.sch]
2016-11-06 Connect mcu to drv8301
    [mcu.sch, power.sch]
2016-11-09 Added LDO for mcu
    [MotCtrl.sch, mcu.sch, power.sch]
2016-11-12 Big changes in power: new mosfets, drivers and current sensing
    [MotCtrl.sch, mcu.sch, power.sch]
2016-11-20 Started working on power supplies
    [MotCtrl.sch, mcu.sch, power.sch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]
2016-11-20 Map INA240 to footprint
    [power.sch]
2016-11-21 Gate power supply enabling and board temp sensor
    [MotCtrl.sch, mcu.sch, power.sch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]
2016-11-22 cleaned out unused footprints
2016-11-22 TVS across bat connection
    [MotCtrl.sch, mcu.sch, power.sch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]
2016-11-23 Bat pads and leds
    [mcu.sch, power_supply.sch]
2016-11-25 Connected and shuffled around mcu pins
    [mcu.sch]
2016-11-26 TVS on 5V and 3.3V rails
    [power_supply.sch]
2016-11-26 Map footprints to components and add BOM
    [BOM_inwork.ods, MotCtrl.sch, mcu.sch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]
2016-11-27 Started playing around with layout
    [power.sch]
2016-11-29 More layout tryouts
    [MotCtrl.kicad_pcb, MotCtrl.sch, mcu.sch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]
2016-11-30 Aligned first power draft
    [MotCtrl.kicad_pcb]
2016-11-30 Alternative layout with smaller total vertical footprint
    [MotCtrl.kicad_pcb, power.sch]
2016-12-01 Yet another alternative
    [MotCtrl.kicad_pcb]
2016-12-03 Go ahead with lower layout
    [MotCtrl.kicad_pcb]
2016-12-03 Som smaller fixes to lower layout
    [MotCtrl.kicad_pcb]
2016-12-03 Started duplicating and aligning power stages
    [MotCtrl.kicad_pcb]
2016-12-07 Aligned, started rework current shunt layout and copper pour
    [MotCtrl.kicad_pcb, MotCtrl.sch, mcu.sch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]
2016-12-10 First draft of power stage placed and routed
    [MotCtrl.kicad_pcb]
2016-12-10 Changed footprint of and placed bulk cap
    [MotCtrl.kicad_pcb, power_supply.sch]
2016-12-11 Placing power supply components
    [MotCtrl.kicad_pcb]
2016-12-11 Changed footprint of hall sensor contact and placed more components
    [MotCtrl.kicad_pcb, mcu.sch]
2016-12-12 Routed power supply
    [MotCtrl.kicad_pcb, mcu.sch]
2016-12-13 Routed EMF and I sense to mcu
    [MotCtrl.kicad_pcb, mcu.sch]
2016-12-13 First draft of completely routed board
    [MotCtrl.kicad_pcb, mcu.sch]
2016-12-15 Forgot some traces...
    [MotCtrl.kicad_pcb, mcu.sch]
2016-12-17 Rounded corners
    [MotCtrl.kicad_pcb]
2016-12-18 Added current sense voltage reference as reparate net again
    [MotCtrl.kicad_pcb, mcu.sch, power.sch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]
2016-12-18 Silkscreen placed correctly
    [MotCtrl.kicad_pcb]
2016-12-18 Add test pads
    [MotCtrl.kicad_pcb, mcu.sch, power.sch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]
2016-12-19 Revision A sent to fab
    [MotCtrl-B.Cu.gbl, MotCtrl-B.Mask.gbs, MotCtrl-B.SilkS.gbo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]
2017-02-10 First version of an elementary BLDC controller
2017-02-18 Change to center-aligned PWM
2017-02-19 Edge aligned PWM. Started to experiment with current and BEMF measurements.
2017-02-26 Changed PWM freq to 20k. Added ability to output sampled values to DAC.
2017-02-26 HW: Changed rc-filter capacitor to increase BEMF-sense bandwidth.
    [BOM_inwork.ods, power.sch]
2017-03-13 0 deg hall offset motor support ONLY
2017-03-18 Work, hall sensor speed measurement
2017-03-18 Reconfigured timer for speed estimation and commutation
2017-03-19 Arbitrary hall sensor offset (0-30 deg) supported
2017-03-20 Determine direction based on current and previous hall state
2017-03-21 Experimenting with angle estimation inbetween hall state changes
2017-03-22 Handle speed timer overflow
2017-04-08 Removed hardcoded DMA instance, partially...
2017-04-08 CRC on tx frames is now possible
2017-04-15 Added measurement of board temp and bat voltage
2017-04-18 Temp measurement sample rate and adc sampling time
2017-04-23 Total current test
2017-04-27 Small restructure of duty flow. Better handling of sample triggering.
2017-04-29 Rename bldc file and functions
2017-05-13 Experimenting with bipolar pwm
2017-06-03 Position refactoring work. Add Encoder as another sensor. Untested.
2017-06-06 Hall-mode tested after position refactoring
